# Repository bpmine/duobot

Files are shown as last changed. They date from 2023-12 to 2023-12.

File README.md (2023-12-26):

# duobot

## Introduction

Ce projet est un n-ième clone du célèbre "self balancing robot" que l'on peut voir un peut partout sur Internet.

Voici un lien vers le projet original: https://electricdiylab.com/diy-self-balancing-robot/

Pour ce projet, nous conservons les fondamentaux de l'original (moteur, drivers, accéléromètre, ...).

Nous utiliserons les matériaux et les outils à notre à notre disposition. Les dimensions du robot seront également les nôtres.

Et la carte sera développée dans le but d'être utilisée pour d'autres applications similaires et pour permettre la mise au point d'autres projets à base de moteurs pas-à-pas.

## Construction du robot

## Conception de la carte

### Schéma

Presque un copier-coller du modèle d'origine.

Les différences principales sont les suivantes:
- Pull up sur le Enable plutôt que des pull-down sur le Step de chaque driver;
- Branchement des M0, M1 et M2 sur l'arduino (pour permettre le réglage de la résolution);
- Possibilité de brancher soit un drv4988 (comme l'original), soit un drv8825 (broche VDD ou Fault que l'on peut connecter grâce à des résistances 0 Ohms);
- Ajout de condensateurs de découplage (comme préconisé dans la datasheet des drivers);
- Sortie des broches non utilisées sur un connecteur d'extension.

### Routage du PCB

Complètement revu pour une carte moins dense (un peu plus grande) de 100mm x 70mm.
Les connecteurs seront des borniers plutôt que des JST comme sur le modèle. Ca permet un peu plus de souplesse lors des essais...

### Vue en 3D

## Mise en service

### Réglage du courant MAX

On tourne le potentiomètre des drivers jusqu'à obtenir 1V. Cela correspond à 250mA environ. Ce réglage sera à afiner en fonction des performances et de la limite admissible par le moteur...

### Programme de test de la carte

Le programme permet de tester la carte.

- Il affiche les valeurs lues sur l'accéléromètre
- il permet d'actionner les moteurs à l'aide des commandes.

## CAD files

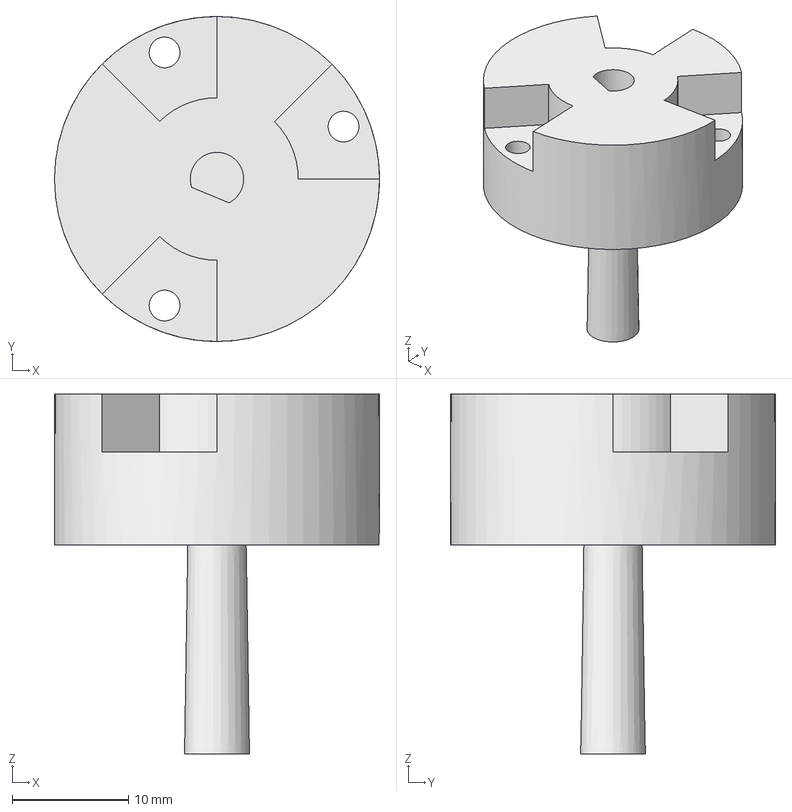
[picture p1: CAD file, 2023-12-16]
mecanique/fixation_roue.FCStd
28.0 x 28.0 x 31.0 mm

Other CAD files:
mecanique/fixation_roue-Body.stl

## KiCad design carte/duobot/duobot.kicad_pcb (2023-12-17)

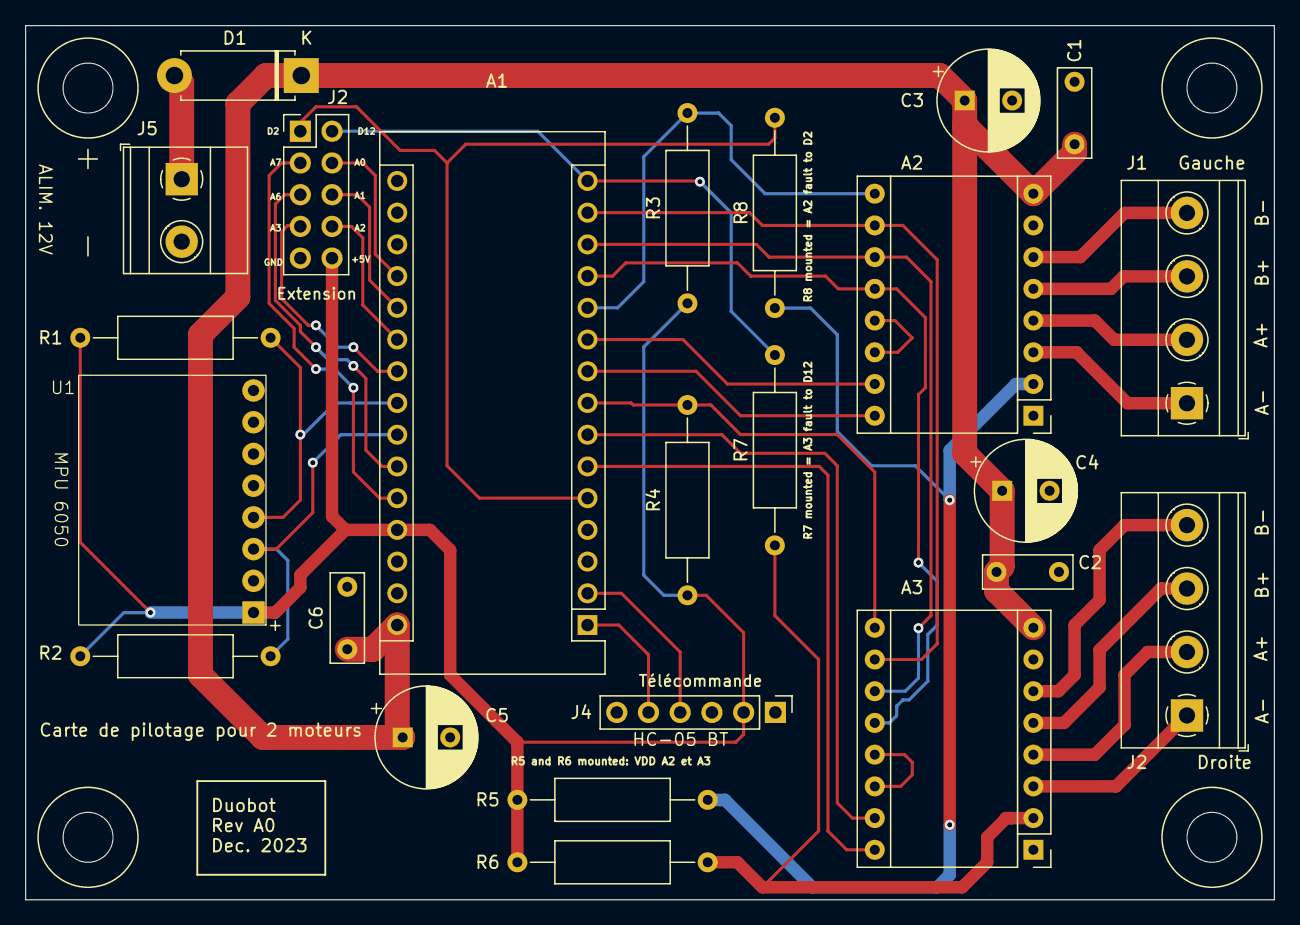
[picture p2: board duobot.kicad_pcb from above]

Board: 2 copper layers, 100.0 x 70.0 mm, 28 parts (0 on the bottom side), 37 nets.

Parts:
A1: Arduino_Nano_v3.x; BPC_Arduino_Nano
A2, A3: BPC_Module-16_15.2x20.3mm
C1, C2: 100n; C_Disc_D7.0mm_W2.5mm_P5.00mm
C3, C4: 100uF; CP_Radial_D8.0mm_P3.80mm
C5: 20uF; CP_Radial_D8.0mm_P3.80mm
C6: 1n; C_Disc_D7.0mm_W2.5mm_P5.00mm
D1: D; D_5W_P10.16mm_Horizontal
J1: Moteur Gauche; TerminalBlock_Phoenix_MKDS-1,5-4-5.08_1x04_P5.08mm_Horizont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
J2: Moteur Droite; TerminalBlock_Phoenix_MKDS-1,5-4-5.08_1x04_P5.08mm_Horizont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
J2#2: Extension; PinHeader_2x05_P2.54mm_Vertical
J4: HC05 - BT; PinHeader_1x06_P2.54mm_Vertical
J5: Batterie; TerminalBlock_Phoenix_MKDS-1,5-2_1x02_P5.00mm_Horizontal
R1, R2: 10k; R_Axial_DIN0309_L9.0mm_D3.2mm_P15.24mm_Horizontal
R3, R4: 100k; R_Axial_DIN0309_L9.0mm_D3.2mm_P15.24mm_Horizontal
R5, R6, R7, R8: 0; R_Axial_DIN0309_L9.0mm_D3.2mm_P15.24mm_Horizontal
U1: BPC_MPU6050
X1, X2, X3, X4: Trou; BPC_Trou4mm_Fixation

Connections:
+5V: A1.27 (+5V), J2#2.10, J4.2, R1.1, R2.2, R3.1, R4.1, R5.2, R6.2, U1.1 (Vcc)
A0: A1.19 (A0), J2#2.4
A1: A1.20 (A1), J2#2.6
A2: A1.21 (A2), J2#2.8
A3: A1.22 (A3), J2#2.7
A6: A1.25 (A6), J2#2.5
A7: A1.26 (A7), J2#2.3
D2: A1.5 (D2), J2#2.1, R8.2
D12: A1.15 (D12), J2#2.2, R7.2
DIR_Droite: A1.6 (D3), A3.16 (DIR)
DIR_Gauche: A1.9 (D6), A2.16 (DIR)
EN_Droite: A1.8 (D5), A3.9 (~ENABLE), R4.2
EN_Gauche: A1.11 (D8), A2.9 (~ENABLE), R3.2
GND: A1.4 (GND), A1.29 (GND), A2.1 (GND), A2.7 (GND), A3.1 (GND), A3.7 (GND), C1.2, C2.2, C3.2, C4.2, C5.2, C6.2, J2#2.9, J4.3, J5.2, U1.2 (Gnd)
M0: A1.14 (D11), A2.10 (MS1), A3.10 (MS1)
M1: A1.13 (D10), A2.11 (MS2), A3.11 (MS2)
M2: A1.12 (D9), A2.12 (MS3), A3.12 (MS3)
unnamed: A1.2 (D0/RX), J4.4
unnamed: A1.1 (D1/TX), J4.5
unnamed: A1.30 (VIN), A2.8 (VMOT), A3.8 (VMOT), C1.1, C2.1, C3.1, C4.1, C5.1, C6.1, D1.1 (K)
unnamed: A2.4 (1A), J1.2
unnamed: A2.3 (1B), J1.1
unnamed: A2.5 (2A), J1.3
unnamed: A2.6 (2B), J1.4
unnamed: A2.2 (VDD), R5.1, R8.1
unnamed: A2.13 (~RESET), A2.14 (~SLEEP)
unnamed: A3.4 (1A), J2.2
unnamed: A3.3 (1B), J2.1
unnamed: A3.5 (2A), J2.3
unnamed: A3.6 (2B), J2.4
unnamed: A3.2 (VDD), R6.1, R7.1
unnamed: A3.13 (~RESET), A3.14 (~SLEEP)
unnamed: D1.2 (A), J5.1
SCL: A1.24 (A5), R2.1, U1.3 (SCL)
SDA: A1.23 (A4), R1.2, U1.4 (SDA)
STEP_Droite: A1.7 (D4), A3.15 (STEP)
STEP_Gauche: A1.10 (D7), A2.15 (STEP)

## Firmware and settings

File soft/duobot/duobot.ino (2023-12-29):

#include <Wire.h>

#define PIN_DIR_DTE     (3)
#define PIN_STEP_DTE    (4)
#define PIN_EN_DTE      (5)
#define PIN_DIR_GHE     (6)
#define PIN_STEP_GHE    (7)
#define PIN_EN_GHE      (8)

#define PIN_M2          (9)
#define PIN_M1          (10)
#define PIN_M0          (11)

#define MPU_ADDR        (0x68)
#define MPU_REG_POWER   (0x6B)
#define MPU_REG_MEASURE (0x3B)

#define MIN_VAL         (265)
#define MAX_VAL         (402)

typedef struct
{
  int pin_enable;
  int pin_dir;
  int pin_step;
  bool is_inverted;
} T_DRV_DEF;

#define DIR_AVANT   (LOW)
#define DIR_ARRIERE (HIGH)

#define MOTOR_GHE   (0)
#define MOTOR_DTE   (1)
const T_DRV_DEF motors[]=
{
  {PIN_EN_GHE, PIN_DIR_GHE, PIN_STEP_GHE, false },
  {PIN_EN_DTE, PIN_DIR_DTE, PIN_STEP_DTE, true }
};


volatile unsigned long g_ulCounter=0;
volatile bool ton=false;
volatile int g_speed=0;
volatile bool g_enabled=false;

inline void pulse_step(int id)
{
  if (g_enabled==false)
  {
    digitalWrite(motors[id].pin_enable,HIGH);
    return;
  }

  digitalWrite(motors[id].pin_enable,LOW);  

  if ( g_speed>=0 )
    digitalWrite(motors[id].pin_dir, motors[id].is_inverted==false ? DIR_AVANT : DIR_ARRIERE);
  else
    digitalWrite(motors[id].pin_dir, motors[id].is_inverted==false ? DIR_ARRIERE : DIR_AVANT);
  
  if ( ( ton==true ) && (g_speed!=0) && (g_enabled==true))
    digitalWrite(motors[id].pin_step,HIGH);    
  else
    digitalWrite(motors[id].pin_step,LOW);
}

ISR(TIMER2_COMPA_vect)
{
  g_ulCounter++;
  
  int cnt=100-min(abs(g_speed),100);
  
  if (ton==false)
  {
    if (g_ulCounter>cnt)
      ton=true;
  }
  else
  {
    g_ulCounter=0;
    ton=false;
  }

  pulse_step(MOTOR_GHE);
  pulse_step(MOTOR_DTE);
}

void init_motor(int id)
{
  digitalWrite(motors[id].pin_enable,HIGH);
  digitalWrite(motors[id].pin_dir,DIR_AVANT);
  digitalWrite(motors[id].pin_step,LOW);
}

void init_timer(void)
{
  cli();
  TCCR2A = 0b00000010;
  TCCR2B = 0b00000110;  ///< Clock/256 pour faire 16us
  TIMSK2 = 0b00000010;
  OCR2A = 10;
  sei();
}

void init_mpu()
{
  Wire.begin();
  Wire.beginTransmission(MPU_ADDR);
  Wire.write(MPU_REG_POWER);
  Wire.write(0);
  Wire.endTransmission(true);
}

int mpu_read_angle(void)
{
  int16_t AcX,AcY,AcZ;
  double x;
  
  Wire.beginTransmission(MPU_ADDR);
  Wire.write(MPU_REG_MEASURE);
  Wire.endTransmission(false);
  Wire.requestFrom(MPU_ADDR,14,true);
  AcX=Wire.read()<<8|Wire.read();
  AcY=Wire.read()<<8|Wire.read();
  AcZ=Wire.read()<<8|Wire.read();
  int xAng = map(AcX,MIN_VAL,MAX_VAL,-90,90);
  int yAng = map(AcY,MIN_VAL,MAX_VAL,-90,90);
  int zAng = map(AcZ,MIN_VAL,MAX_VAL,-90,90);
  
  x= RAD_TO_DEG * (atan2(-yAng, -zAng)+PI);

  if (x>360)
    x=360;
    
  if (x>120)
    return -(360-x);
  else
    return x;
}

void setup() 
{
  Serial.begin(115200);
  Serial.println("BOOT Duobot.");

  pinMode(PIN_DIR_DTE,OUTPUT);
  digitalWrite(PIN_DIR_DTE,LOW);
  pinMode(PIN_STEP_DTE,OUTPUT);
  digitalWrite(PIN_STEP_DTE,LOW);
  pinMode(PIN_EN_DTE,OUTPUT);
  digitalWrite(PIN_EN_DTE,HIGH);

  pinMode(PIN_DIR_GHE,OUTPUT);
  digitalWrite(PIN_DIR_GHE,LOW);
  pinMode(PIN_STEP_GHE,OUTPUT);
  digitalWrite(PIN_STEP_GHE,LOW);
  pinMode(PIN_EN_GHE,OUTPUT);
  digitalWrite(PIN_EN_GHE,HIGH);

  pinMode(PIN_M0,OUTPUT);
  digitalWrite(PIN_M0,HIGH);
  pinMode(PIN_M1,OUTPUT);
  digitalWrite(PIN_M1,HIGH);
  pinMode(PIN_M2,OUTPUT);
  digitalWrite(PIN_M2,HIGH);

  init_mpu();
  init_motor(MOTOR_GHE);
  init_motor(MOTOR_DTE);
  init_timer();
}

void serialEvent()
{  
  int cmd=Serial.read();
  if (cmd=='a')
  {
    Serial.println("AV gauche");
    g_enabled=true;
    g_speed=abs(g_speed);
  }
  else if (cmd=='q')
  {
    Serial.println("Stop");
    g_enabled=false;
  }
  else if (cmd=='w')
  {
    Serial.println("AR gauche");
    g_enabled=true;
    g_speed=-abs(g_speed);
  }
  else if (cmd=='0')
  {
    Serial.println("Speed 0");
    g_speed=0;
  }
  else if (cmd=='1')
  {
    Serial.println("Speed 1");
    g_speed=1;
  }
  else if (cmd=='2')
  {
    Serial.println("Speed 2");
    g_speed=20;
  }
  else if (cmd=='3')
  {
    Serial.println("Speed 3");
    g_speed=50;
  }
  else if (cmd=='4')
  {
    Serial.println("Speed 4");
    g_speed=80;
  }
  else if (cmd=='5')
  {
    Serial.println("Speed 5");
    g_speed=100;
  }
}

void loop() 
{
  unsigned long t=millis();
  
  delay(1000);

  int ang=mpu_read_angle();
  Serial.print("Angle: ");
  Serial.println(ang);

  /*if (ang>2)
  {
    g_enabled=true;
    g_speed=10;
  }
  else if (ang<-2)
  {
    g_enabled=true;
    g_speed=-10;
  }
  else if (abs(ang)>=2)
  {
    g_enabled=true;
  }
  else
  {
    g_enabled=false;
  }*/
}

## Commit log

2023-12-16 Création pièce pour fixation roue
    [fixation_roue-Body.stl, fixation_roue.FCStd]
2023-12-17 Création de la carte de pilotage du robot
    Empreintes de l'accéléromètre et du module bluetooth à revoir avant envoi
    [duobot.kicad_pcb, duobot.kicad_sch]
2023-12-17 Finalisation routage et schéma
    [duobot.kicad_pcb, duobot.kicad_sch]
2023-12-17 Correction suite analyse des règles PCB
    [duobot.kicad_pcb]
2023-12-26 Carte: Petite correction référence R5 et R8 sur le schéma Création du programme de test de la carte: OK
    [duobot.kicad_sch]
2023-12-29 Création du soft de pilotage du robot
    - Pilotage des moteurs sous IT (même vitesse des deux côtés)
    - mesure angle d'inclinaison
    Reste à faire le PiD....
